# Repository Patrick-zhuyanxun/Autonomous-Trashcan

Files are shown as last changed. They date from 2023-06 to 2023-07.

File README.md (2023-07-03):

# Autonomous-Trashcan

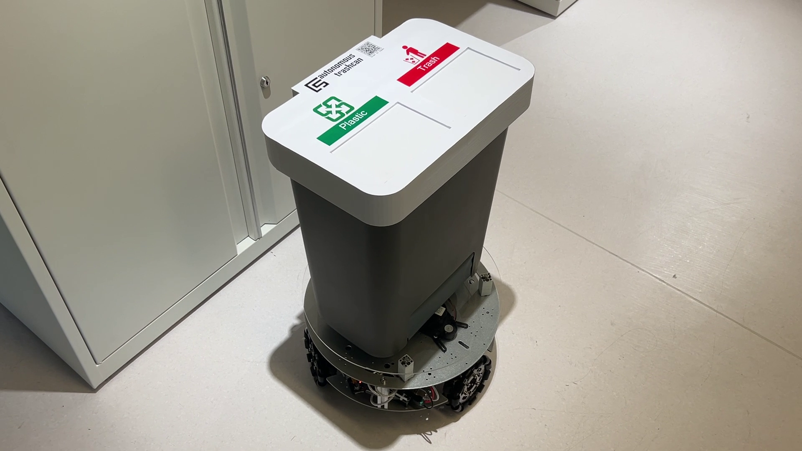
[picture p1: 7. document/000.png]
https://github.com/Patrick-zhuyanxun/Autonomous-Trashcan/7.document/000.png))


## 0.Introduction

此專案由「國立臺北科技大學 城市科學實驗室 2023 Spring UROP」開發。

### 0-1 範例影片:

https://youtu.be/4PowflGdkpY

### 0-2 動機

         台灣每年產生的垃圾量是逐年在增長的，從2001年的800萬噸，到2023以增長到1123萬噸。且根據統計，在2018年時，已經有20.4萬噸的垃圾是無法處理的，到了2021年，甚至成長到了67.9萬噸。

         本組希望透過此自動垃圾桶，使用者能夠對於在公眾場合製造的垃圾量有認知，針對回收給予回饋金以促進回收率，搭配移動底盤增加使用者的便利性。

### 0-3 使用方式

總共有3種方式可以丟垃圾

### 0-3-1 定點呼叫

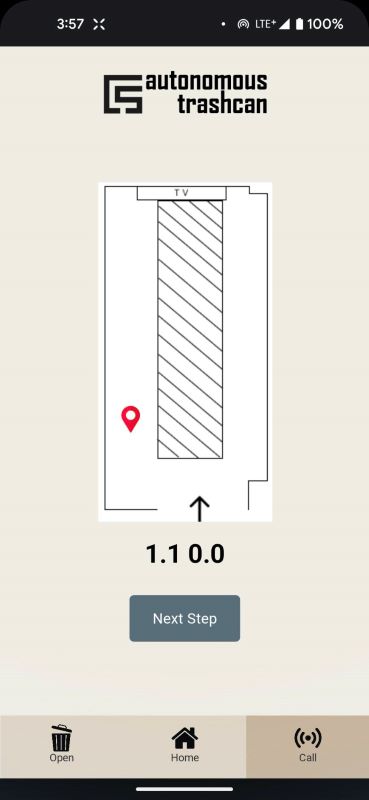
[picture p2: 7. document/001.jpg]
https://github.com/Patrick-zhuyanxun/Autonomous-Trashcan/7.document/001.jpg))


### 0-3-2 按鈕開啟

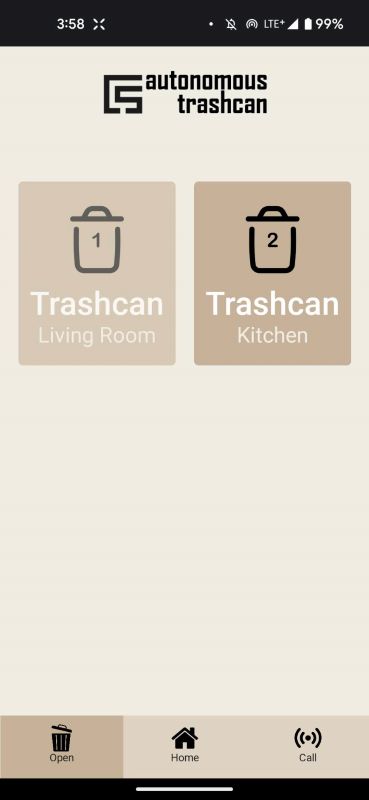
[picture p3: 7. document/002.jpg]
https://github.com/Patrick-zhuyanxun/Autonomous-Trashcan/7.document/002.jpg))


### 0-3-3 掃描qr code

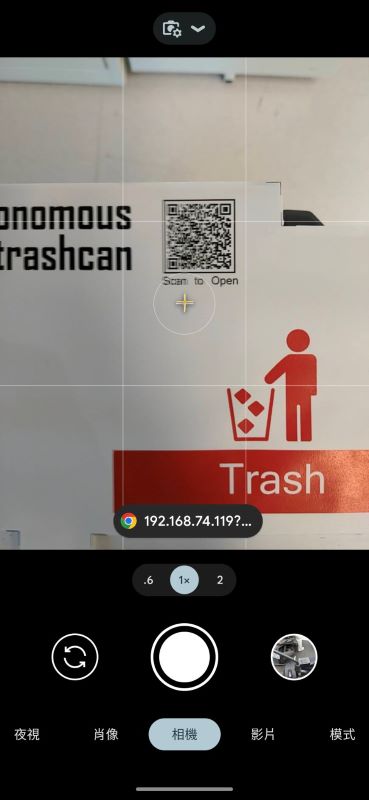
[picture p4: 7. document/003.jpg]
https://github.com/Patrick-zhuyanxun/Autonomous-Trashcan/7.document/003.jpg))


## 1. Mechanism

   本次硬體構造分為底盤部分與垃圾桶部分，首先介紹底盤部分:

### 1-1 底盤部分:

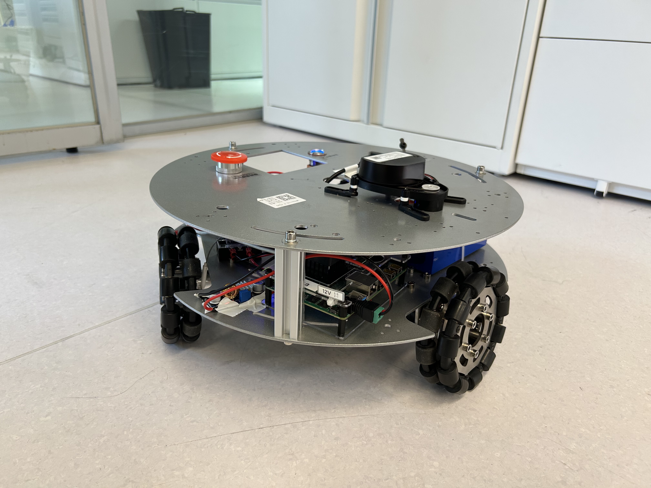
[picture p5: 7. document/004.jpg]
https://github.com/Patrick-zhuyanxun/Autonomous-Trashcan/7.document/004.jpg))


(1) 選用**輪趣科技**所推出之圓形常規[高配版全向輪機器人](https://wheeltec.net/product/html/?176.html)，底盤直徑為390mm，負重能力為15kg，後期在上方又加上一塊厚度3mm之壓克力板，將垃圾桶固定於底盤上方。

(2) 車體之主控版為udoo推出之[X86 II](https://www.udoo.org/docs-x86II/Introduction/Introduction.html)主機板，於車體上加裝一24 to 12V降壓器供電給主控板使用。

(3) 車上搭載之LIDAR型號為LDS-01，使用官方驅動。

### 1-2 垃圾桶

   將垃圾桶分為蓋子與主體兩塊部分進行說明:

1-2-1 **主體:**

  選用IKEA 的****[KNÖCKLA](https://www.ikea.com.tw/zh/search/?q=KN%C3%96CKLA)****垃圾桶進行改裝，容量為25公升型，內部有兩個內桶，可以放置兩種不同類型之垃圾或回收，並在垃圾桶底部開孔，安裝重量感測器量測垃圾重量。

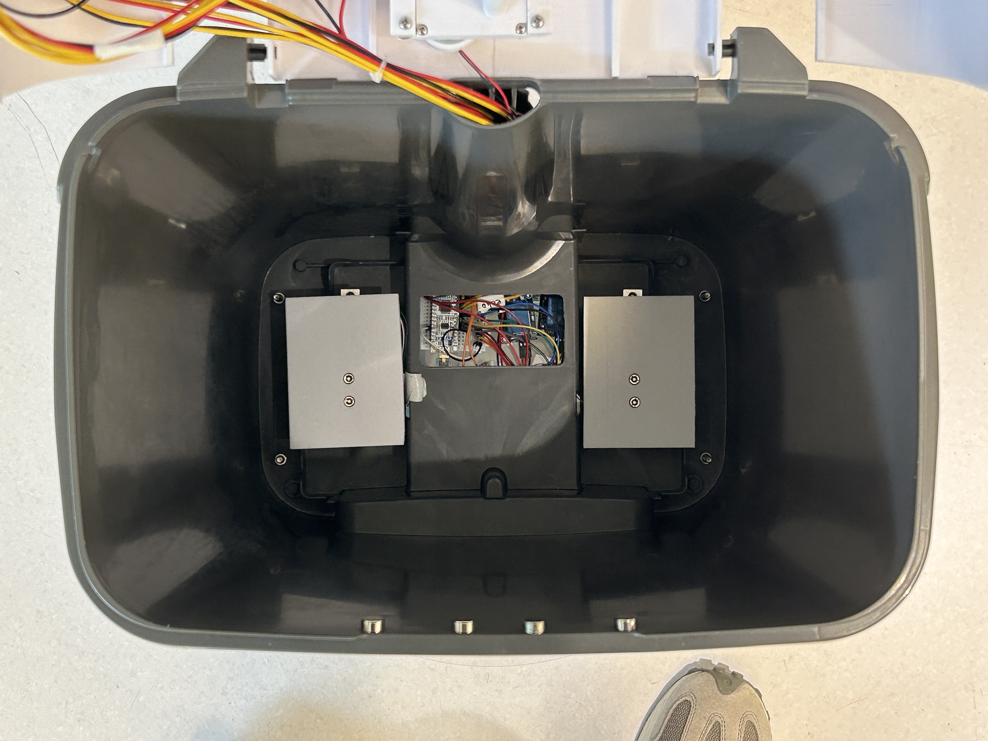
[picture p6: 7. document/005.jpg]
https://github.com/Patrick-zhuyanxun/Autonomous-Trashcan/7.document/005.jpg))


1-2-2 **蓋子:**

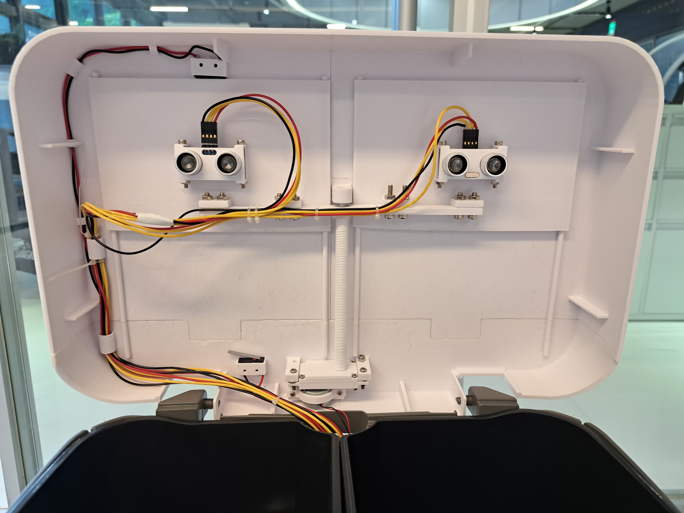
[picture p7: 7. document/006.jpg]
https://github.com/Patrick-zhuyanxun/Autonomous-Trashcan/7.document/006.jpg))


(1) 蓋子實體圖如上圖，整體皆以3d列印製作而成，上方搭載了兩顆HC-SR04超聲波感測模組，用以量測垃圾桶容量。

(2) 開關蓋板作動方式則是透過馬達帶動螺桿轉動藉此帶動整體蓋板前後開合，並且在兩端位置加入極限開關，以達到限位的目的。

(3) 馬達選用一般常見之RF310發電機馬達，並透過自行設計之齒輪組(模數0.5，雙層齒輪，齒輪比1.0*2.4*3.0=7.2)達到降低轉速，增加扭矩之目的。

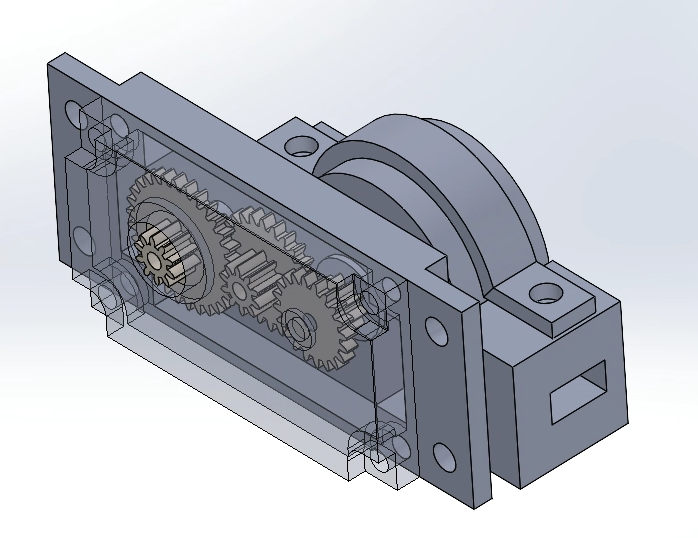
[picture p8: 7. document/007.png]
https://github.com/Patrick-zhuyanxun/Autonomous-Trashcan/7.document/007.png))


## 2. Hardware

### 2-1 垃圾桶蓋電路
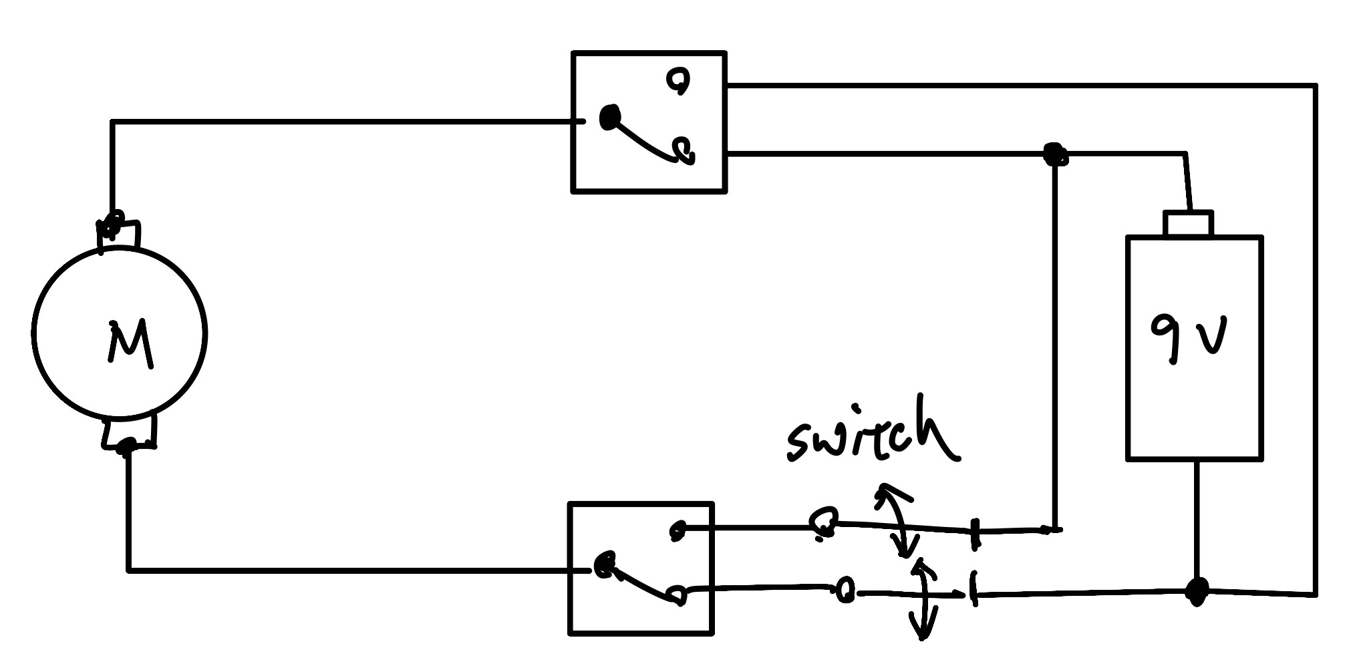
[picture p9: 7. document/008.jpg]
https://github.com/Patrick-zhuyanxun/Autonomous-Trashcan/7.document/008.jpg))


### 2-2 垃圾桶硬體架構

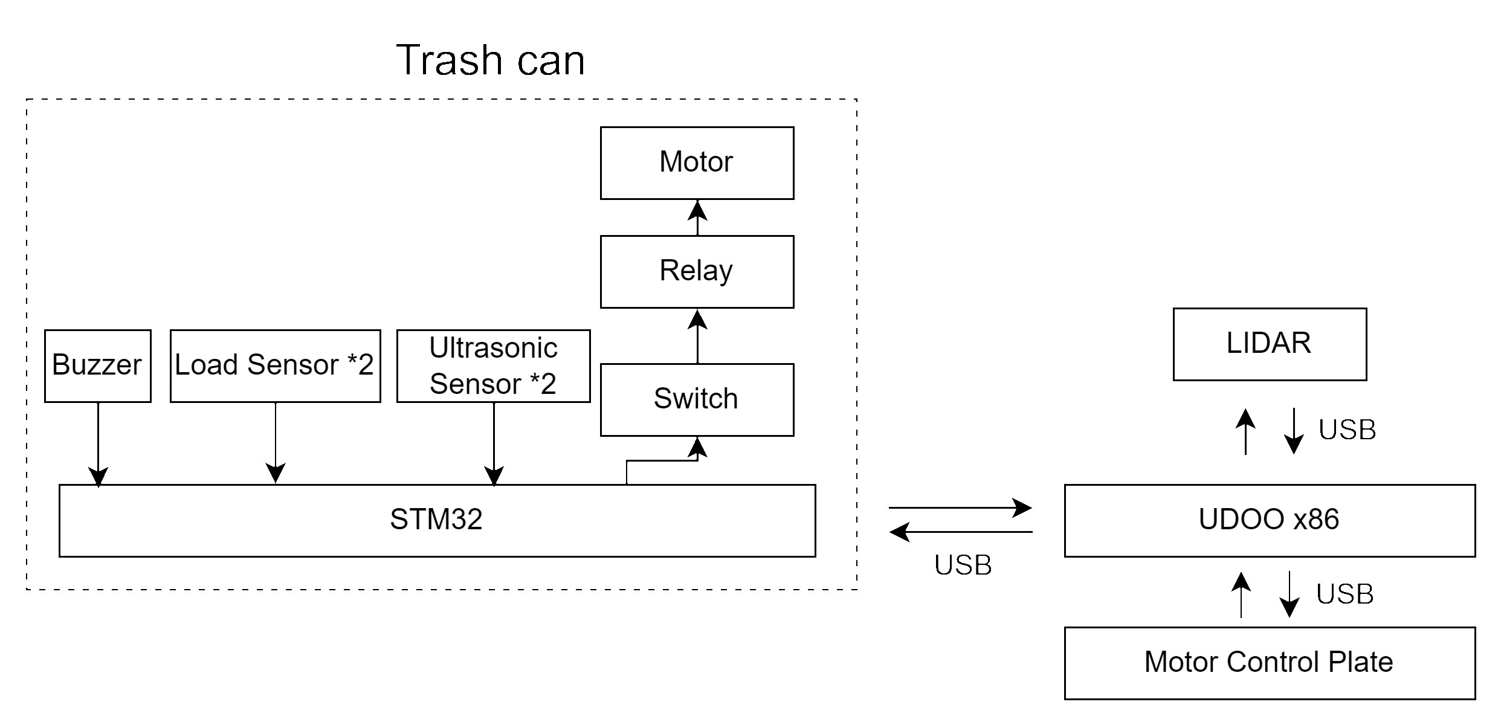
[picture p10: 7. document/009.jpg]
https://github.com/Patrick-zhuyanxun/Autonomous-Trashcan/7.document/009.jpg))


### 2-3 使用之感測器、元件型號總整理

|  | 型號 | 數量 | 說明or購買網址 |
| --- | --- | --- | --- |
| 主控版 | UDOO X86 II | 1 | https://www.udoo.org/docs-x86II/Introduction/Introduction.html |
| LIDAR | LDS-01 | 1 | https://emanual.robotis.com/docs/en/platform/turtlebot3/appendix_lds_01/ |
| STM32 | STM32 Nucleo | 1 |  |
| Motor | RF310 | 1 |  |
| Ultrasonic Sensor | HS-SR04 | 2 |  |
| Load Sensor | 搭配晶片：HX711 | 2 | https://www.jin-hua.com.tw/webc/html/product/show.aspx?num=33618&kind=2686 |
| Limit Switch | KW11-3Z | 2 | https://www.jin-hua.com.tw/webc/html/product/show.aspx?num=2099&kind=1566 |

## 3. Front_end

使用React框架進行網站建設

### 3-1 執行前端server

Step1:使用VScode開啟Front_end資料夾

Step2:開啟terminal並cd進入’trashcan_newer_frontend’

Step3:下載下方API並指定版本

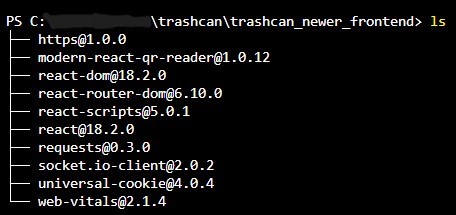
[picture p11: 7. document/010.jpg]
https://github.com/Patrick-zhuyanxun/Autonomous-Trashcan/7.document/010.jpg))


Step4:輸入’npm start’，前端server開始運行

### 3-2 與Socket, Django server進行連線

由於本組的設定，前端只需與Socket進行連線

trashcan_newer_fronted/src/socket.js

上方路徑的檔案中

將網址換成使用者使用的Socket server的IP及Port即可

```jsx
const socket = io.connect("http://192.168.74.156:4040");
```

### 注意

若未與socket, django server進行連線，則無法完成login

## 4. trashcan_stm32

(1) 本次開發stm32韌體使用Arduino IDE進行開發

(2) 設定偏好路徑：https://github.com/stm32duino/BoardManagerFiles/raw/main/package_stmicroelectronics_index.json

(3) 選擇工具/開發板：

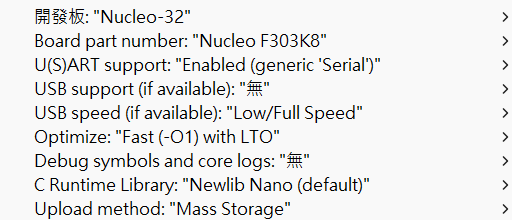
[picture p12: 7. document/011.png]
https://github.com/Patrick-zhuyanxun/Autonomous-Trashcan/7.document/011.png))


(4) 編譯並燒錄即可

## 5. Django

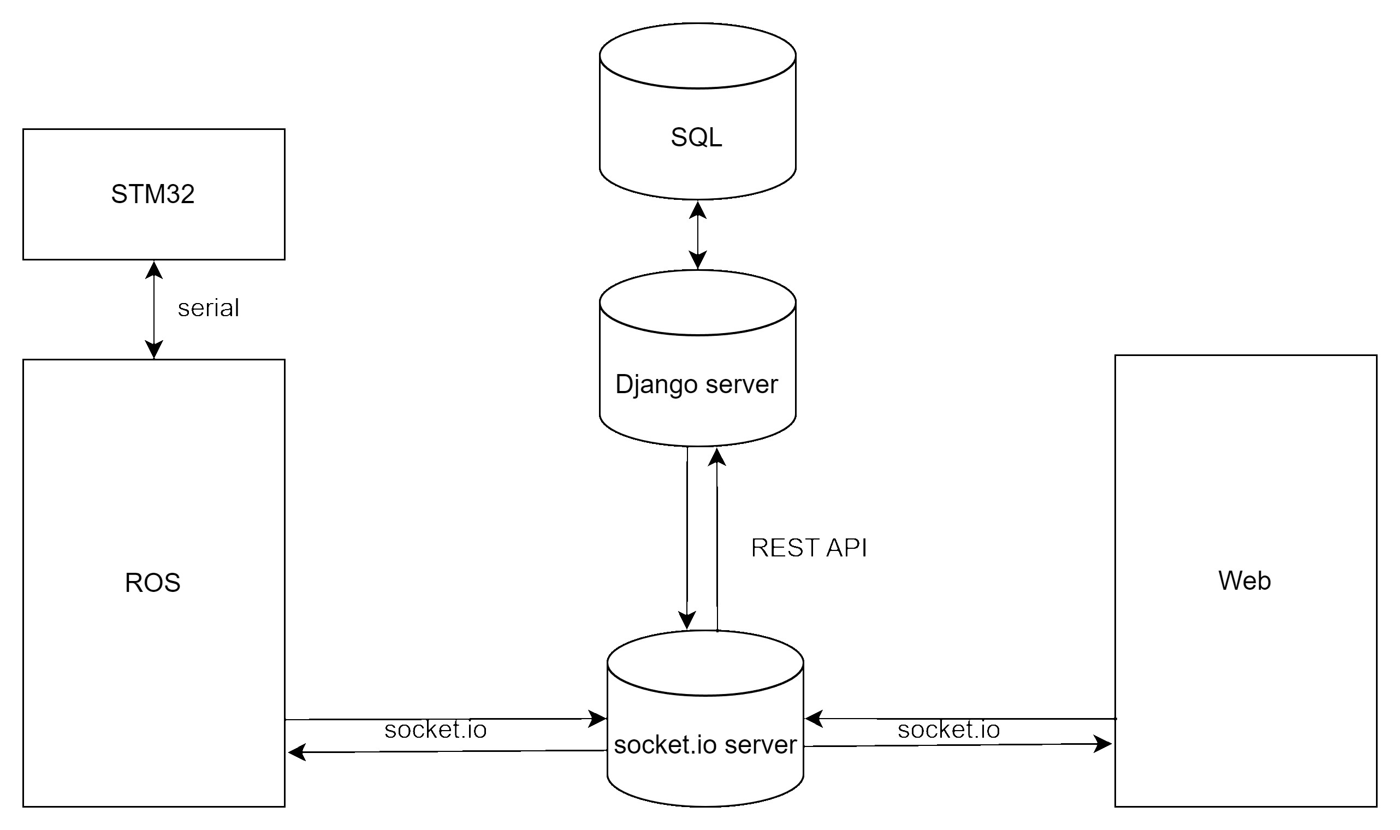
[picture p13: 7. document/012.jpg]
https://github.com/Patrick-zhuyanxun/Autonomous-Trashcan/7.document/012.jpg))


### Version

django==4.1.7

### 5-1 執行 Django server

cmd先進入到Database所在資料夾

```bash
cd "/yourpath/4. Django/Database"
```

(1) 執行Django server (url為127.0.0.1:8000)

```bash
python manage.py runserver 
```

(2) 執行Django server (url為your_ip:8000)

```bash
python manage.py runserver 0.0.0.0:8000
```

### 注意

若使用(2)方法，請確認網路連線為「私人網路」。

設定方式(win 11)：網路和網際網路>WiFi>”your wifi” 屬性>網路設定檔類型點選「私人網路」

### 5-2 檔案說明

server/models.py : 資料庫格式設定

server/models : 定義各功能

Database/urls.py: 定義各API的網址

## 6.  ROS

### 6-1 導航設定

(1) 修改LIDAR座標：ROS/src/turn_on_wheeltec_robot/launch/robot_model_visualization.launch (car_model: mini_omni)

(2) 建圖：

roslaunch ROS/src/turn_on_wheeltec_robot/launch/mapping.launch

啟動新終端cd到ROS/src/turn_on_wheeltec_robot/map

rosrun map_server map_saver -f $檔案名稱

(3) 啟動導航與連線：

進入ROS/src/turn_on_wheeltec_robot/launch/navigation.launch修改地圖路徑

roslaunch ROS/src/turn_on_wheeltec_robot/launch/navigation.launch 同時啟動導航與socketio連線

### 6-2 與socketio連線

修改src\turn_on_wheeltec_robot\scripts\trashcan_main.py

line 151 改為socketio server的IP

### 6-3 與stm32連線

修改 src\turn_on_wheeltec_robot\scripts\trashcan_main.py

line 32 改為stm32的串口名稱

若無法開啟請給予串口權限

## 7. Socket_server

(1) 若為Windows系統，請確認網路連線為「私人網路」。

(2) 修改程式中IP位址，包含Django Server的IP (line 6)與自己的IP(line 160)。

(3) 確認版本，測試使用python-socketio==4.6.1, python-engineio==3.14.2, JavaScript Socket.IO==2.0.2, requests==2.28.2

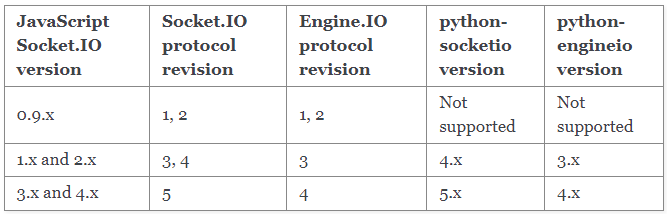
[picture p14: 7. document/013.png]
https://github.com/Patrick-zhuyanxun/Autonomous-Trashcan/7.document/013.png))

## 8. API格式
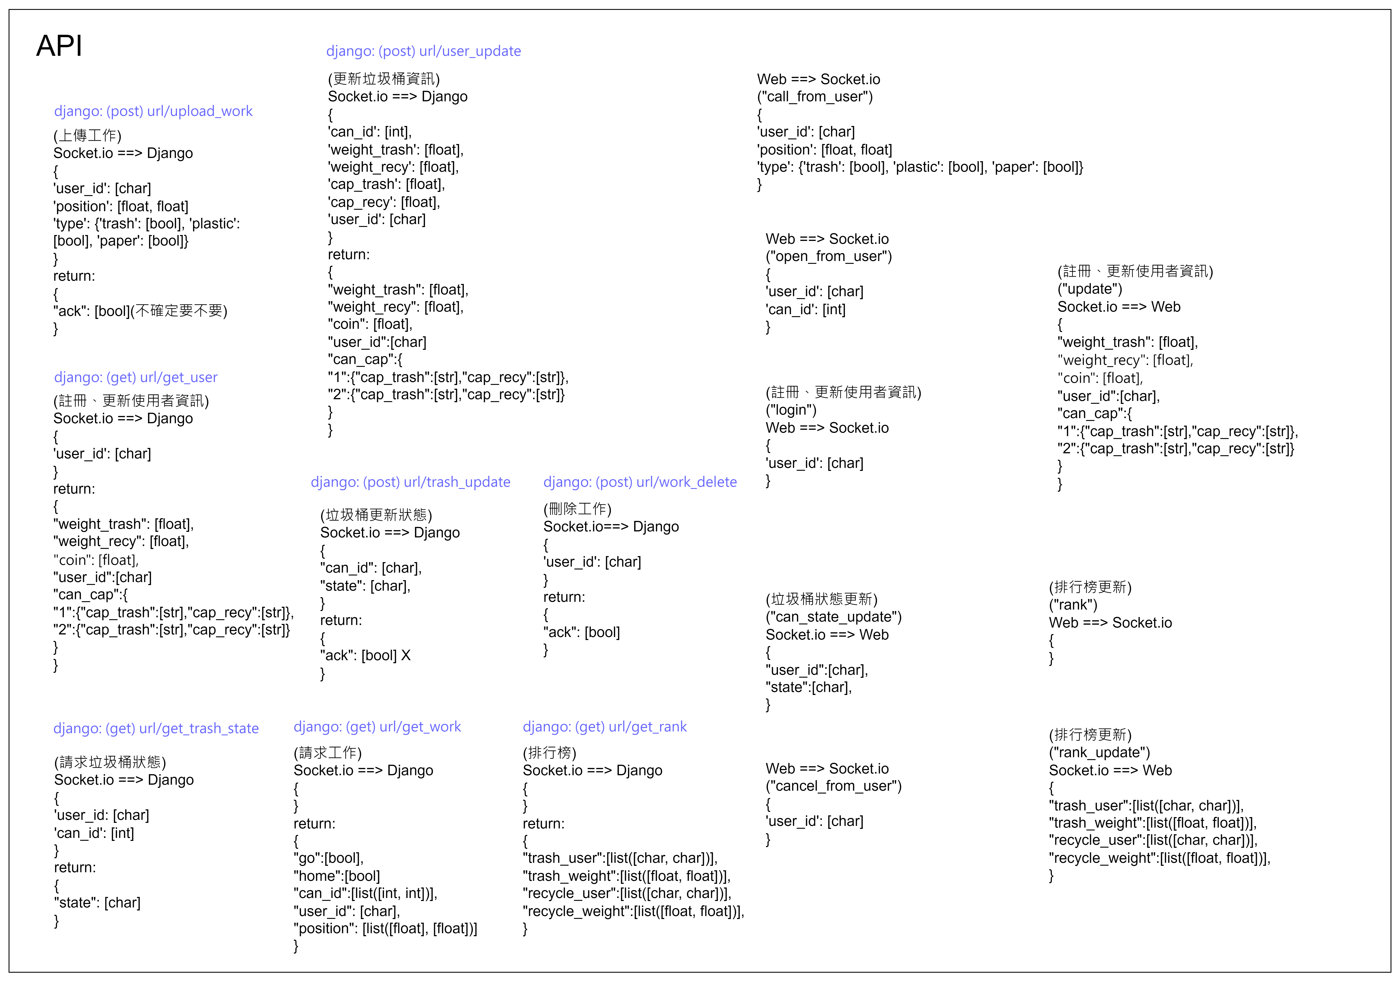
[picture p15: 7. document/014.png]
https://github.com/Patrick-zhuyanxun/Autonomous-Trashcan/7.document/014.png))


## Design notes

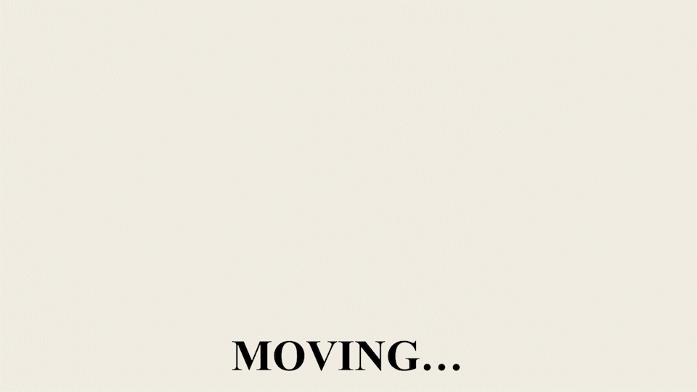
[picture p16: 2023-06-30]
2. Front_end/trashcan_newer_frontend/src/assets/moving.gif

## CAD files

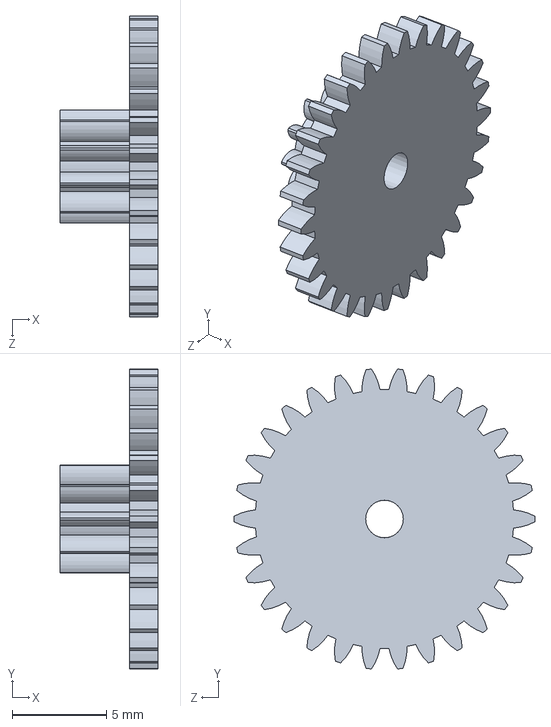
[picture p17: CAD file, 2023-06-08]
1. CAD_file/Autonomous-Trashcan/GEAR.SLDASM
5.20 x 15.9 x 16.0 mm
spur gear_iso x 2

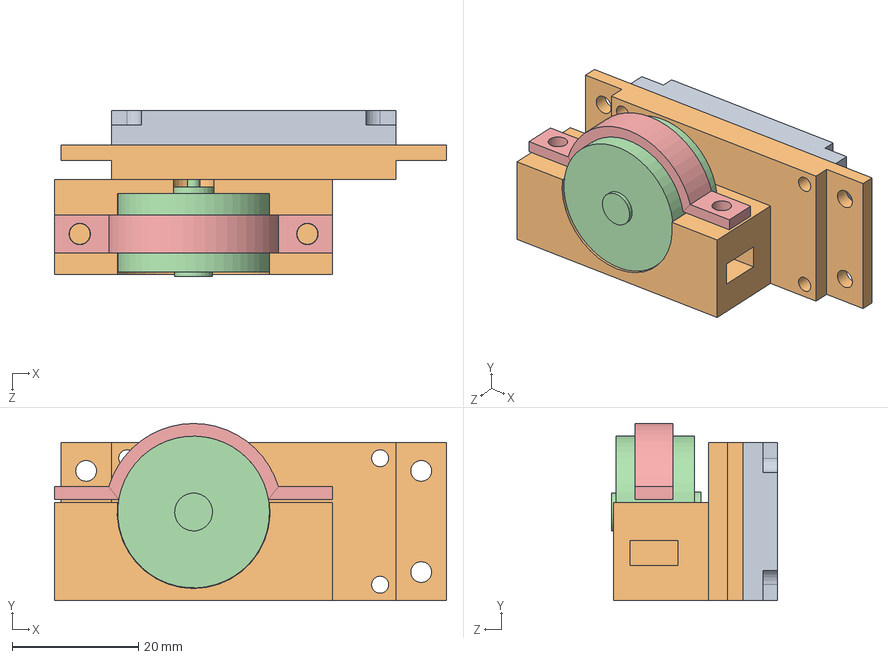
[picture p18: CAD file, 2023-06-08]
1. CAD_file/Autonomous-Trashcan/gearbox.SLDASM
62.0 x 28.0 x 26.2 mm
gear_box
spur gear_iso x 2
small_motor
固定
gear_board

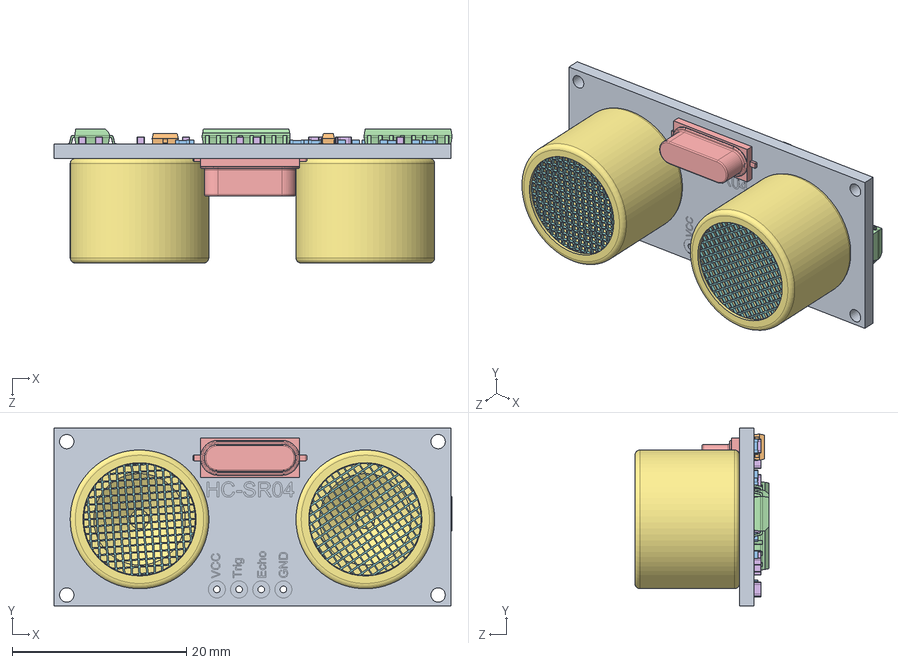
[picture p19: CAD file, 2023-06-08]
1. CAD_file/Autonomous-Trashcan/HC-SR04.SLDASM
45.6 x 20.4 x 15.4 mm
Board.stp
SOT23.stp x 2
0603 Resistor.stp x 21
SOIC16 narrow.stp x 3
Crystal Oscillator (SMD).stp
0603 Capacitor.stp x 17
Transducer.stp
Mesh.stp x 2

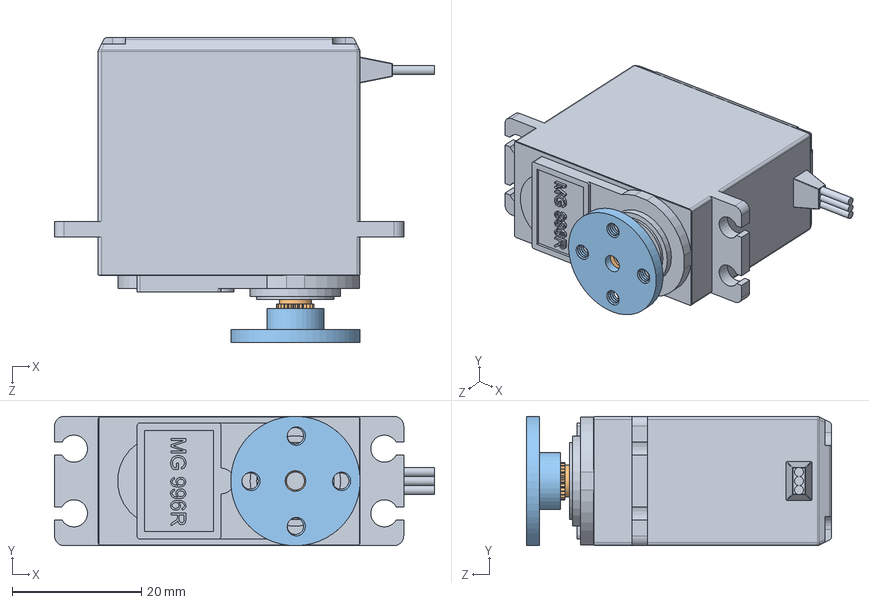
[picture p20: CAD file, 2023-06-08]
1. CAD_file/Autonomous-Trashcan/MG996 v1 v12_v6.SLDASM
58.8 x 20.0 x 47.1 mm
servo body^MG996 v1 v12(2)_MG996 v1 v12
TowerPro-MG995_pulley v1^MG996 v1 v12(2)_MG996 v1 v12
複製 of servo dise v1^MG996 v1 v12(2)_MG996 v1 v12

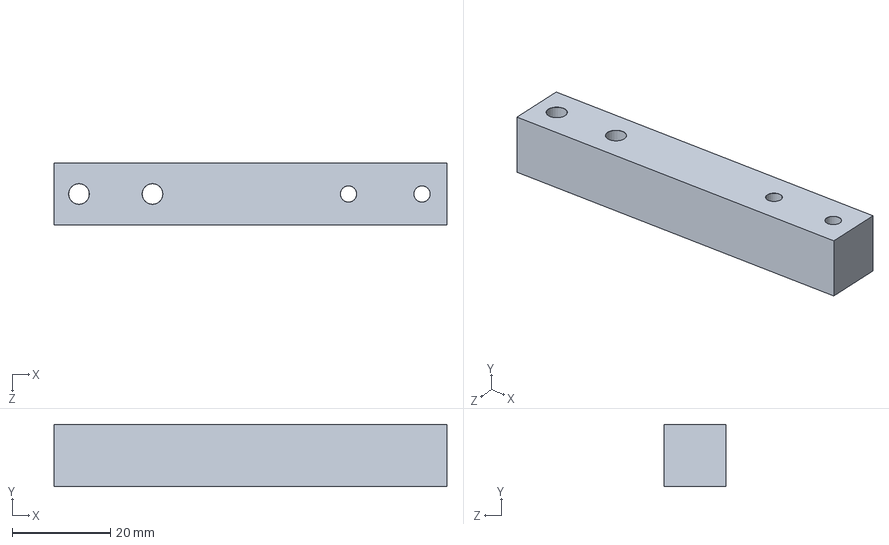
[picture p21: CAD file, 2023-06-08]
1. CAD_file/Autonomous-Trashcan/load_sensor_with_board.SLDASM
80.2 x 12.7 x 12.7 mm

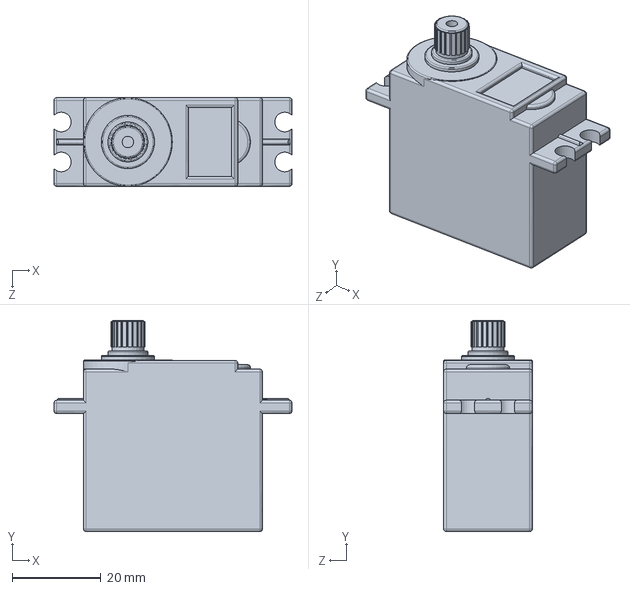
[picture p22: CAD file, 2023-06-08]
1. CAD_file/Autonomous-Trashcan/Servo MG996R.SLDPRT
53.6 x 47.6 x 20.0 mm

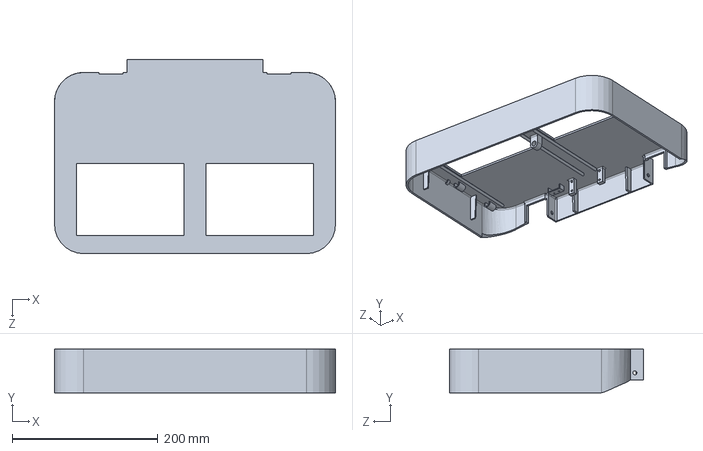
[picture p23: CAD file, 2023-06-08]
1. CAD_file/Autonomous-Trashcan/上蓋_small_v6.SLDPRT
386.2 x 60.0 x 267.0 mm

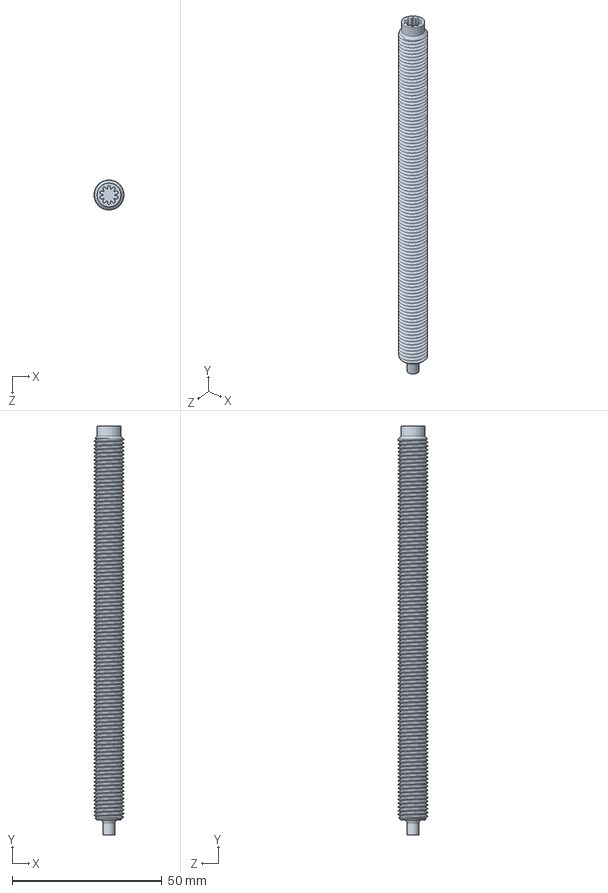
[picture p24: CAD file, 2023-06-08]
1. CAD_file/Autonomous-Trashcan/螺桿.SLDPRT
10.0 x 136.7 x 10.00 mm

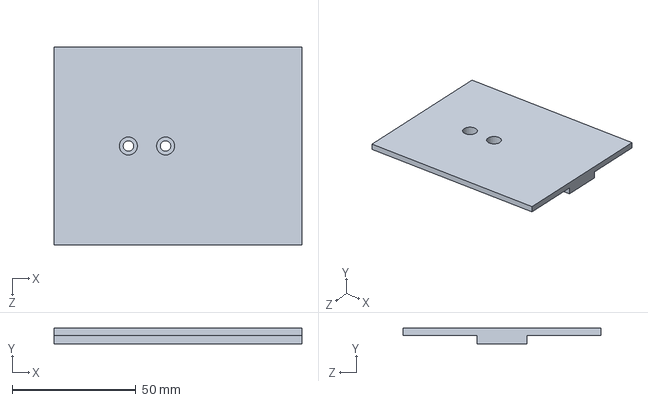
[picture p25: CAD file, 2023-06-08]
1. CAD_file/Autonomous-Trashcan/底板.SLDPRT
100.0 x 6.40 x 80.0 mm

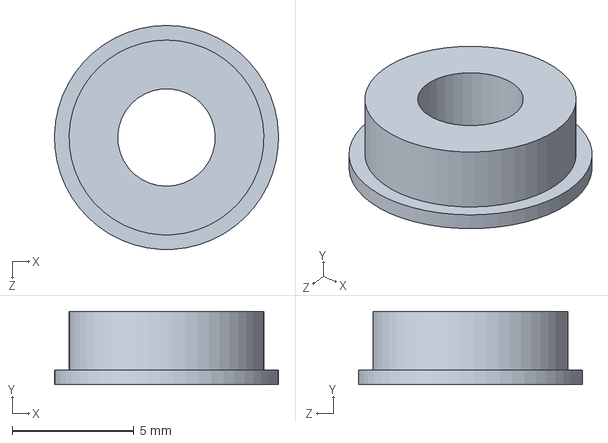
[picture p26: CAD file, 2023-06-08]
1. CAD_file/Autonomous-Trashcan/bearing.SLDPRT
9.20 x 3.00 x 9.20 mm

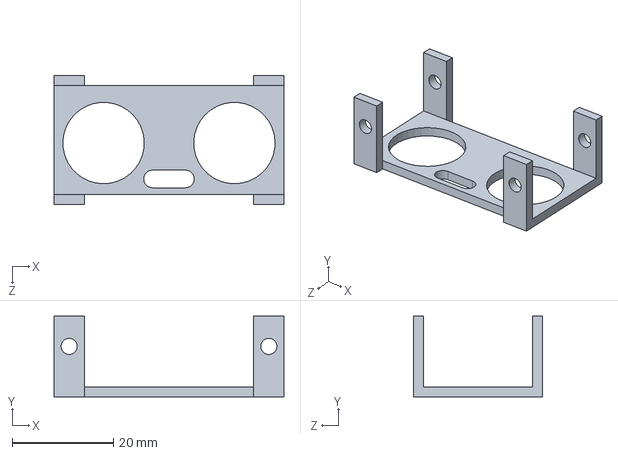
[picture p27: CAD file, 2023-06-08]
1. CAD_file/Autonomous-Trashcan/hcsr04_固定架.SLDPRT
45.5 x 16.0 x 25.5 mm

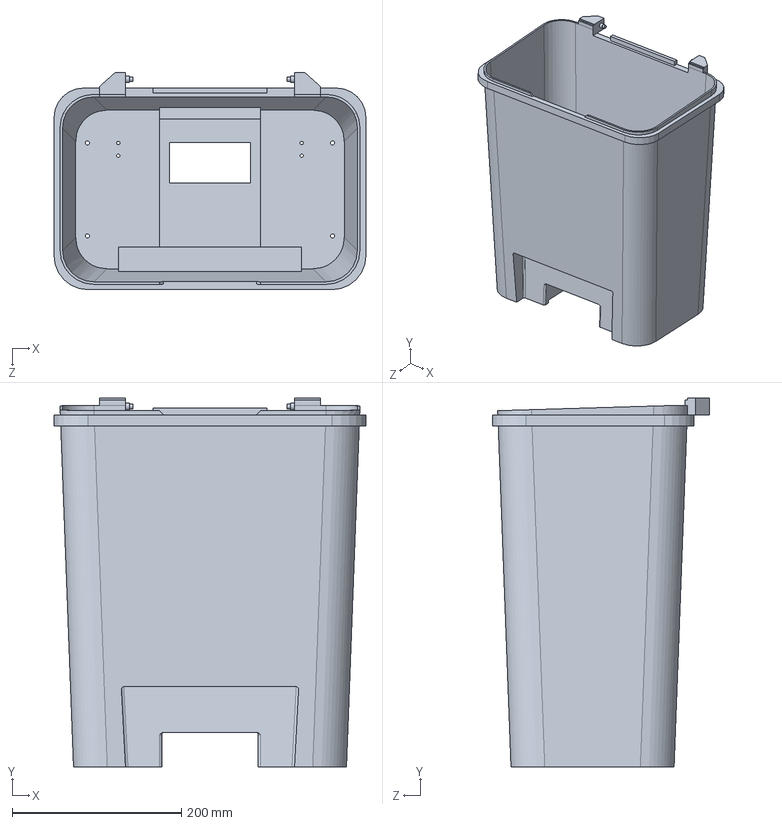
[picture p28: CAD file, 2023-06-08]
1. CAD_file/Autonomous-Trashcan/bin_small.SLDPRT
369.0 x 436.5 x 257.0 mm

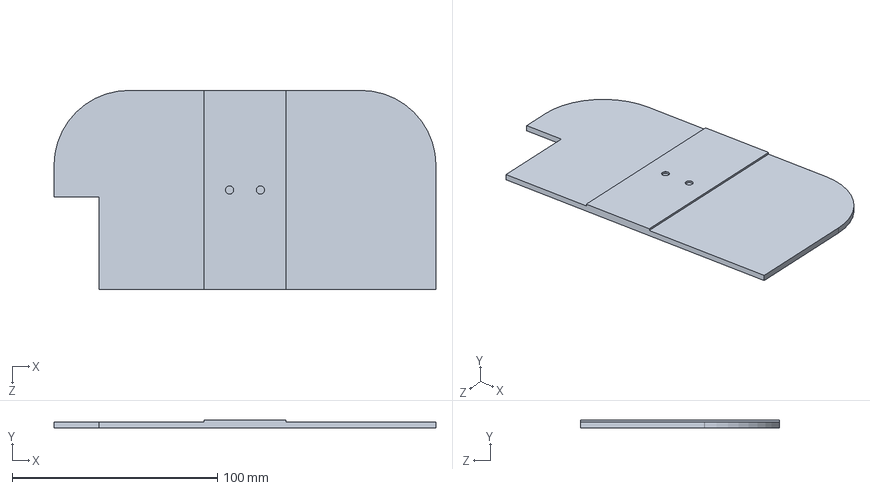
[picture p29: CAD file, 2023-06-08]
1. CAD_file/Autonomous-Trashcan/load_board.SLDPRT
186.0 x 4.00 x 97.0 mm

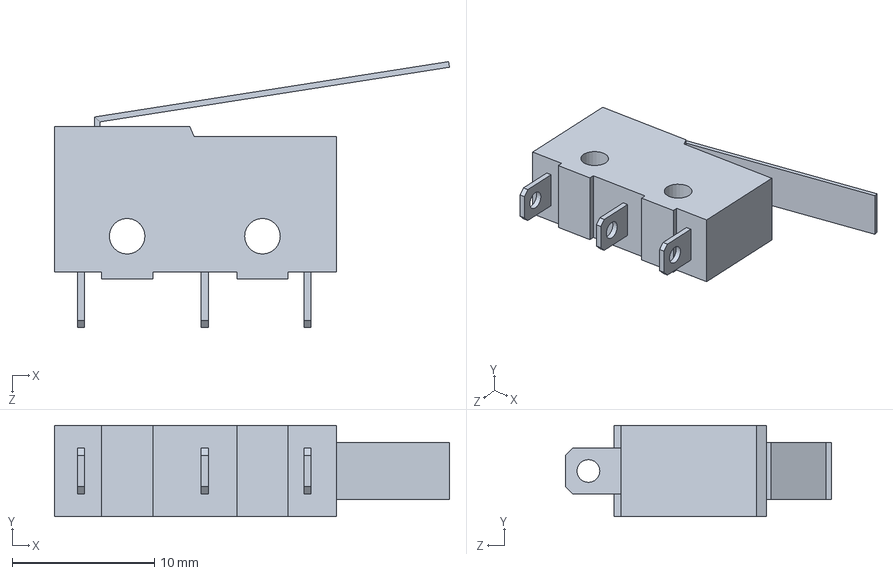
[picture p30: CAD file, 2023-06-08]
1. CAD_file/Autonomous-Trashcan/stop_switch.SLDPRT
27.7 x 6.40 x 18.7 mm

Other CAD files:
1. CAD_file/Autonomous-Trashcan/Servo Bracket - universal v10_v6.SLDASM
1. CAD_file/Autonomous-Trashcan/Servo Bracket - universal v10.SLDASM
1. CAD_file/Autonomous-Trashcan/gear_board.SLDPRT
1. CAD_file/Autonomous-Trashcan/固定.SLDPRT
1. CAD_file/Autonomous-Trashcan/gear_box.SLDPRT
1. CAD_file/Autonomous-Trashcan/load_sensor.SLDPRT
1. CAD_file/Autonomous-Trashcan/small_motor.SLDPRT
1. CAD_file/Autonomous-Trashcan/socket head cap screw_iso.sldprt
1. CAD_file/Autonomous-Trashcan/top_board.SLDPRT
1. CAD_file/Autonomous-Trashcan/螺帽part.SLDPRT

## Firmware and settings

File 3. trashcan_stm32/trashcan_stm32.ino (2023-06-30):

#include "Servo.h"   //載入函式庫，這是內建的，不用安裝
#include "ArduinoJson.h"
#include "HX711.h"
//pin setting
//HC-SR04
const byte trigPin_1 = D6; //超音波測距的 觸發腳
const byte echoPin_1 = D7; //超音波測距的 回應腳
const byte trigPin_2 = D8; //超音波測距的 觸發腳
const byte echoPin_2 = D9; //超音波測距的 回應腳
//hx711
const int DT_PIN_1 = D2;   //重量感測器1
const int SCK_PIN_1 = D3;
const int DT_PIN_2 = D4;   //重量感測器2
const int SCK_PIN_2 = D5;

const int buzzerPin = D11;
const int motorPin = D10;

const int scale_factor_1 = 437; //比例參數，從校正程式中取得 左
const int scale_factor_2 = 446; //比例參數，從校正程式中取得 右

int CAN_ID=1;   //trashcan id
String command;
int trash_weight=0;
int recycle_weight=0;
int opentime_count=0;
int change_count=0;
int trash_bias = 0;
int recycle_bias = 0;

HX711 scale_1; // 建立load sensor物件
HX711 scale_2;

void setup() {
  Serial.begin(9600);
  pinMode(trigPin_1, OUTPUT);
  pinMode(echoPin_1, INPUT); 
  pinMode(trigPin_2, OUTPUT);
  pinMode(echoPin_2, INPUT); 
  pinMode(buzzerPin, OUTPUT);
  pinMode(motorPin, OUTPUT);
  scale_1.begin(DT_PIN_1, SCK_PIN_1);
  scale_2.begin(DT_PIN_2, SCK_PIN_2);
  scale_1.set_scale(scale_factor_1);       // 設定比例參數
  scale_2.set_scale(scale_factor_2);       // 設定比例參數
  scale_1.tare();               // 歸零
  scale_2.tare();               // 歸零
}

void loop() {   
  while (Serial.available()){
    command = Serial.readString();
    //傳送重量
    if(command == "open"){    
      digitalWrite(motorPin, HIGH);   //trashcan open
      delay(5500);
      scale_1.tare();               // 歸零
      scale_2.tare();               // 歸零
      tone(buzzerPin, 523);
      delay(100);
      tone(buzzerPin, 784);
      delay(200);
      noTone(buzzerPin);
      while(true){
        opentime_count += 1;
        recycle_weight = scale_1.get_units(10)*(-1);
        trash_weight = scale_2.get_units(10)*(-1);
        //Serial.print(trash_weight);
        //Serial.print(",");
        //Serial.println(recycle_weight);
        if((trash_weight>3)or(recycle_weight>3)){   //計算重量改變次數
          change_count += 1;
        }
        else{
          change_count = 0;
        }
        if((change_count>5)or(opentime_count==60)){   //重量改變或超過秒數關閉垃圾桶
          change_count = 0;
          tone(buzzerPin, 784);
          delay(100);
          tone(buzzerPin, 523);
          delay(200);
          noTone(buzzerPin);
          if(trash_weight<4){
            trash_weight = 0;
          }
          if(recycle_weight<4){
            recycle_weight = 0;
          }
          break;
        }
      }
      
      //capcity
      int cap_recycle = sr04(trigPin_1, echoPin_1) * 0.017; 
      int cap_trash = sr04(trigPin_2, echoPin_2) * 0.017;
      digitalWrite(motorPin, LOW);  //trashcan close
      delay(5000);
      // Create the JSON document
      StaticJsonDocument<200> doc;
      doc["can_id"] = CAN_ID;
      doc["weight_trash"] = trash_weight;
      doc["weight_recy"] = recycle_weight;
      doc["cap_trash"] = cap_trash;
      doc["cap_recy"] = cap_recycle;
      // Send the JSON document over the "link" serial port
      serializeJson(doc, Serial);
      Serial.println();
    }
  }
}


//超音波測距函式  
//送 10μs 脈波給 HC-SR04 觸發腳(trigger pin)，並計算 回應腳(echo)變成高電位的時間
unsigned long sr04(const byte trigPin, const byte echoPin) { 
  digitalWrite(trigPin, HIGH);
  delayMicroseconds(10);  
  digitalWrite(trigPin, LOW);
  return pulseIn(echoPin, HIGH);
}

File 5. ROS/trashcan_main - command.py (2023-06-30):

#!/usr/bin/env python
# license removed for brevity
import rospy
from std_msgs.msg import String
import socketio
import json
import serial
import time
import re
from geometry_msgs.msg import PointStamped, PoseStamped
from move_base_msgs.msg import MoveBaseActionResult

# sudo chmod 666 /dev/ttyACM2    #open port

CAN_ID = 1
DEBUG = False

sio = socketio.Client()

if DEBUG == False:
	connection = serial.Serial('/dev/ttyACM1', baudrate=9600) # connect to STM32
	connection.reset_input_buffer()

############################## publisher ##############################

pub = rospy.Publisher('/move_base_simple/goal', PoseStamped, queue_size=10) # geometry_ms/PoseStamped
#pub = rospy.Publisher('chatter', String, queue_size=10)
rospy.init_node('talker', anonymous=True) # create a rosnode 
rate = rospy.Rate(10) # 10hz
USER='0'   # initial user id
POSITION = [0.0,0.0]    # initial user position


def main():

    @sio.event
    def connect():
        print('Connected to server')

    @sio.event
    def disconnect():
        print('Disconnected from server')

    # moving require from user
    @sio.event
    def moving_req(can_id, user_id, position):
        global USER
        global POSITION
        USER = user_id
        POSITION = position
        print(POSITION, USER)
        if(can_id == CAN_ID):
        # moving to user position
            sio.emit('can_state', {'can_id': CAN_ID, 'state': 'moving'})
            print('rsp (can_state)===> socket', {'user_id':user_id, 'can_id': CAN_ID, 'state': 'moving'})
            pose = PoseStamped()
            pose.header.frame_id = 'map'
            pose.pose.position.x = position[0]
            pose.pose.position.y = position[1]
            pose.pose.orientation.z = 0.0
            pose.pose.orientation.w = 1.0
            print('rsp (/move_base_simple/goal)', pose) 
            talker(pose) 

    # open trash can require from user
    @sio.event
    def open_req(user_info):
        if(user_info['can_id'] == CAN_ID):
            open_trashcan(user_info['user_id'])

    def open_trashcan(user_id):
        # open trash can
        sio.emit('can_state', {'user_id':user_id, 'can_id': CAN_ID, 'state': 'opening'})
        print('rsp (can_state)===> socket', {'user_id': user_id, 'can_id': CAN_ID, 'state': 'opening'})
        command = 'open'    # serial send "open"
        if DEBUG == False:
            connection.write(command.encode())
        print('rsp (serial)==> stm32', command)
        # return by serail
        while True:
            if DEBUG == False:
                data = connection.readline() #.decode("utf-8")
                try:
                    data = json.loads(data)
                    print('stm32 (serial)==> rsp', data)
                    data['user_id']=user_id
                    break
                except:
                    print("except error", data)
                    data = data[:-2]
                    #data = data.replace("u'","\{\"")
                    data = "{" + data
                    print("except error2", data)
                    data = json.loads(data)
                    print('stm32 (serial)==> rsp', data)
                    print("except error", data)
                    data['user_id']=user_id
                    break
            else:
                time.sleep(10)
                data = {'can_id':1, 'weight_trash':11,'weight_recy':22, 'cap_trash': 33.33, 'cap_recy': 44.44, 'user_id': user_id}
                break

        # update can data
        sio.emit('can_data', data)  
        print('rsp (can_data)===> socket', data)
        # update state
        time.sleep(2)
        sio.emit('can_state', {'user_id':user_id, 'can_id': CAN_ID, 'state': 'stop'})
        print('rsp (can_state)===> socket', {'user_id':user_id, 'can_id': CAN_ID, 'state': 'stop'})

    def goal_result_callback(result):
        print("in goal_result_callback")
        position = POSITION
        if result.status.status == result.status.SUCCEEDED:     # check whether robot reach goal succesfully
            rospy.loginfo("Goal reached successfully!")
            print(position) 
            if((position[0] != 0.0)|(position[1] != 0.0)):  # check whether robot are on the original point
                open_trashcan(USER)
            else:
                sio.emit('can_state', {'user_id':USER, 'can_id': CAN_ID, 'state': 'stop'})
        else:
            rospy.loginfo("Navigation failed!")
            sio.emit('can_state', {'user_id':USER, 'can_id': CAN_ID, 'state': 'failed'})
            time.sleep(2)
            sio.emit('can_state', {'user_id':USER, 'can_id': CAN_ID, 'state': 'stop'})

    def talker(send):
        print("in talker")
        rospy.loginfo(send)
        pub.publish(send)
        rate.sleep()
        #rospy.Subscriber('/move_base/result', MoveBaseActionResult, goal_result_callback)
    sub  = rospy.Subscriber('/move_base/result', MoveBaseActionResult, goal_result_callback)    # subscribe /move_base/result
    
    sio.connect('http://192.168.74.156:4040') # socket.io client connect to server 
    sio.wait()
 
if __name__ == '__main__':
    main()

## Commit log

2023-06-08 upload cad file
    [GEAR.SLDASM, HC-SR04.SLDASM, MG996 v1 v12_v6.SLDASM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]
2023-07-01 更新readme
2023-07-01 更新圖片
2023-07-01 新增圖片
